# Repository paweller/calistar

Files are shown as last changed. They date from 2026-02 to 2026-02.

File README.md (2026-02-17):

# Calistar and Calitower Z

Check out the [wiki](https://github.com/dirtdigger/fleur_de_cali/wiki) for a step-by-step guide to Calistar! Calitower Z functions just the same way.

# Calistar (formerly Fleur de Cali)

Two examples 120x3 and 100x2 example

This is a free, open source, parametric tool used for adjusting the dimensional correctness and skew of your printer. This model performs a similar function to other prints such as Califlower, but has no relation to nor has been derived from any part of those. Turns out that the math behind printer skew calibration has been around since Euclid, and its application to 3D printers is well-documented on other open source project's websites like Klipper. Getting the best performance out of your printer shouldn't be behind a paywall.

Parameters you can control within the Cadquery source code:

- Number of measure points for each axis, up to 5 (default 3)
- Thickness of the grid separator pieces (default is 4mm)
- Total width of the print (default 120)
- Height of the print (default 4mm)

Features:

- Parametric design. Try this with other calibration prints: scale up the model by 20%. You'll find your print time and material used increase by up to 50% since the thickness of the print also increases. Using this design, load up a different stl to keep the thickness the same. Your print time and material used only increase by about 20%
- Bigger is better. No calipers are perfect. Printing larger calibration prints decreases the relative error of your measurements. Included is up to 180mm full size, but make sure you've got calipers that can go that large before printing.
- Multiple measurement points. Measure as many locations as you want up to three times. If you get bored of measuring, stop. If you only want to measure two outermost points since they give the highest signal-to-noise ratio, do that. The spreadsheet is smart enough to figure it out. Just make sure for every outer measurement you have a corresponding inner measurement to offset incorrect flow calibration.
- Know when to stop. Along with offsets, error estimation based on the variance of your measurements and the error in your calipers are provided. If you're probably fixing noise, the spreadsheet will tell you.

Stl and step files that are included are all 4mm tall and have varying thickness depending on the size of the print. The files are named calistar_{print width}x{number of measurements per axis}.stl.

Note about Enders and other budget printers: the movement on the x-axis is non-linear, [see here](https://klipper.discourse.group/t/correct-dimensional-accuracy/6093/5) for discussion on the matter. Calistar works on the principle that movement in each axis is linear, and therefore cannot be used to calibrate the dimensional accuracy of such printers. However, it _can_ be used to calculate and fix your printer's skew.

# Calitower Z - an addition to Calistar

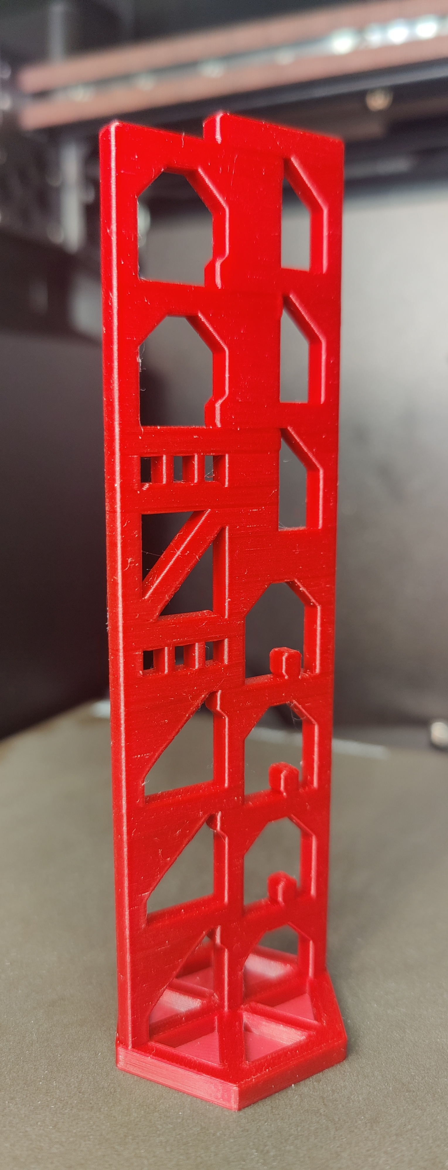
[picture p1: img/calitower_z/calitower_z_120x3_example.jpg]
Calitower Z example


Just as Calistar, Calitower Z is a free, open source, and parametric tool used to adjust a 3D printer's dimensional accuracy. While Calistar calibrates the x- and y-axis, Calitower Z sets out to do exactly that, just for the 3D printer's z-axis. Calitower Z was inspired by Calistar and is designed based on Calistar's core principles. Simply transfer the knowledge gained about Calistar to Calitower Z and you will be good to go to get your 3D printer's z-axis dialed in. Note that Calitower Z does not support a z-axis scew calibration.

__Notes on Printing__

- Use a layer height of 0.2 mm (or 0.1 mm). Otherwise, the nominal distance values between two measurement points are not guaranteed to be 120 mm, 80 mm, and 40 mm!
- Use the correct Calitowre Z version for the type of printed filament.
    - Rather stiff polymers (PLA, PETG, ABS, ASA, PC, Nylon, etc.) can easily be printed without any stiffening support structure. The correct files are the "calitower_z_stiff_<...>.<file_type>".
    - Flexible polymers (TPU, PEBA, etc.) require stiffening support structure. The correct files are the "calitower_z_flex_<...>.<file_type>".

__Notes on measuring__

- While the outer measurements are likely to represent the 3D printer's calibration quite accurately, the inner measurements might not. Even though bridging sections are kept at a minimum distance, their measurements are likely not 100 % accurate. The reasons are two-fold:
    - The droop will be ever so slight.
    - The extruded filament does not get squished against an underlying layer, but can radially extend almost equally in all directions.
    - Nevertheless, when handling these measurements diligently and taking one or two more samples per pair of measurment points, the results should be quite precise. That is at least what empirically showed.

__Notes on provided files__

- Calitower Z is currently only available in a 120x3 version. So a nominal 120 mm measurement height (144 mm print height required) with three distances for outer and inner measurements, respectively
- All the .step and .stl files provided in this repository can also be found on [printables.com](https://www.printables.com/model/1600089-calitower-z-an-addition-to-the-open-source-calista). Additionally, .3mf project as well as .bgcode presliced print files are available there.
- Regarding the calibration worksheets for Calitower Z kindly refer to the section [Browser-based calibration worksheet](#browser-based-calibration-worksheet).

# Browser-based calibration worksheet

The web-based calibration worksheet is Markdown that has been written to be compiled with [Material for Mkdocs](https://squidfunk.github.io/mkdocs-material/). A compiled version is available on [Printables](https://www.printables.com/model/778188-calistar-parametric-open-source-alternative-to-cal), simply unzip `calistar_browser.zip` and open `index.html` in a web browser.  

Note for the Calitower Z: Currently, only the "Parametric Skew Calibration.xlsx" has been modified to include dedicated input sections and output values for the z-axis. However, the browser-based version can be used just as well. Simply enter the z-measurements into either the x or y value sections and leave the rest empty. The results shown for the corresponding axis now refer to the z-axis.

# Excel-based calibration worksheet

An Excel-based calibration worksheet is included in the repo. It was created in Google Sheets, and has been tested in Excel and LibreOffice Calc. Using it with any other spreadsheet tool is unsupported and may result in errors that will not be addressed.

# License

Calistar source code and stls are distributed under GPL3 license. 

[jSpreadsheets](https://github.com/jspreadsheet/ce), [jSuites](https://github.com/jsuites/jsuites), and [Plotly Javascript](https://plotly.com/javascript/is-plotly-free/) libraries are also included in the repository, and are re-distributed under the MIT license.

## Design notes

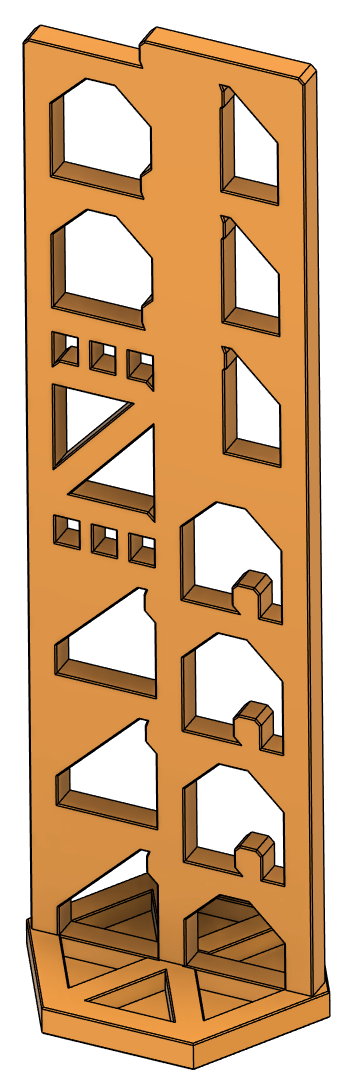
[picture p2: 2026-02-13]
img/calitower_z/calitower_z_stiff_render.png

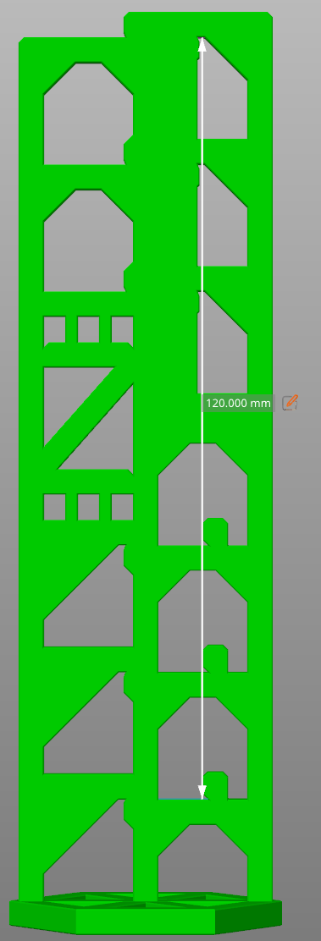
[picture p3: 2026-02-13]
img/calitower_z/calitower_z_inner_z1.png

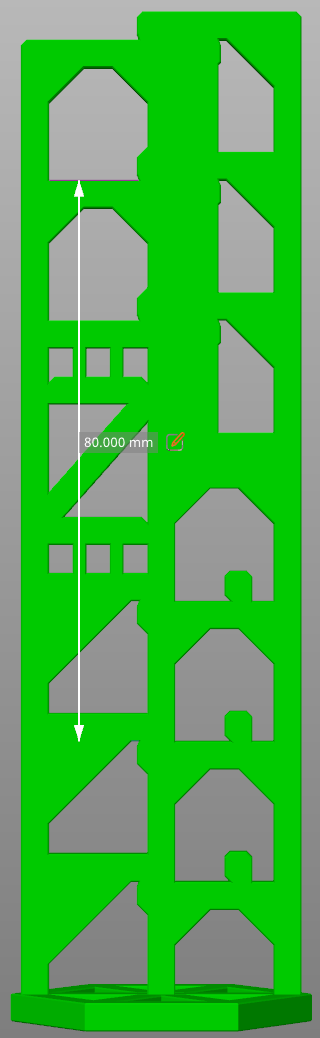
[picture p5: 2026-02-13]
img/calitower_z/calitower_z_outer_z2.png

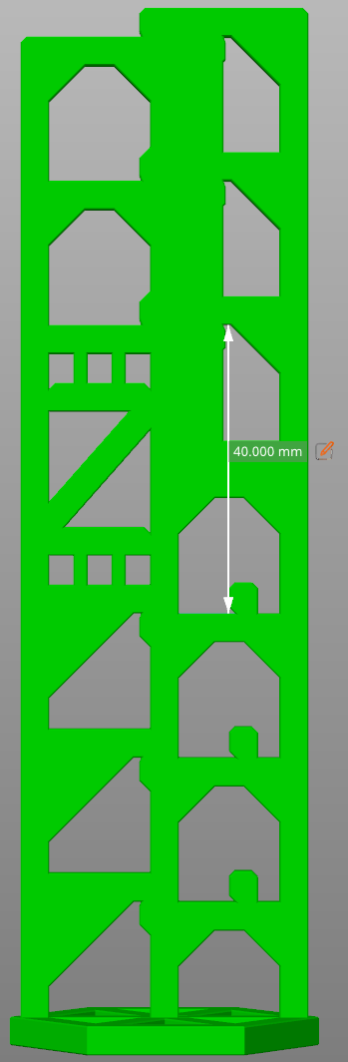
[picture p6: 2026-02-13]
img/calitower_z/calitower_z_inner_z3.png

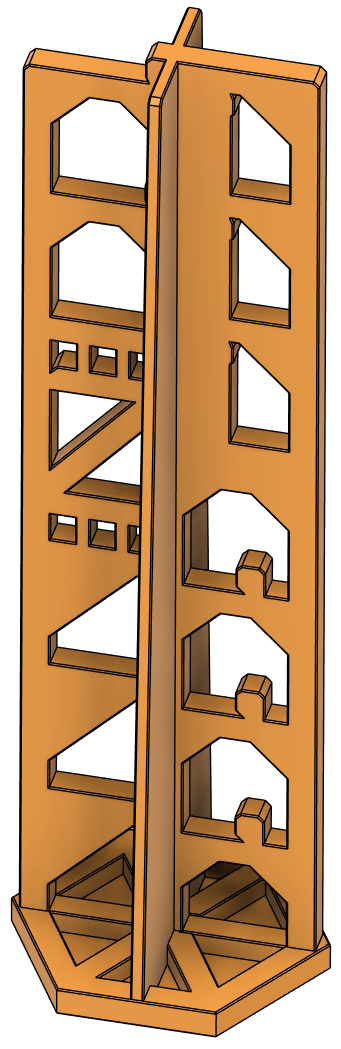
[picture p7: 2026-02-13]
img/calitower_z/calitower_z_flex_render.png

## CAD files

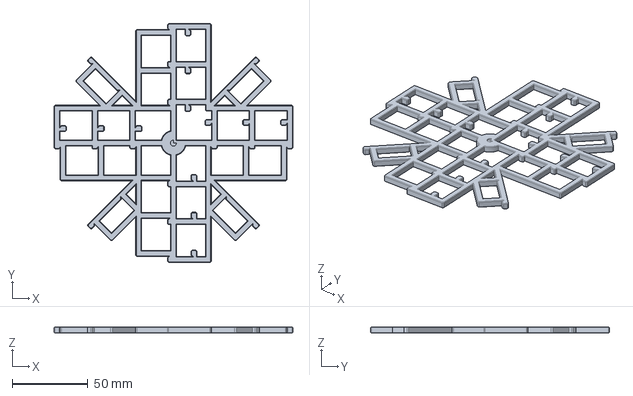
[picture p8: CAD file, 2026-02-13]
step/calistar/calistar_150x3.step
158.0 x 158.0 x 4.00 mm

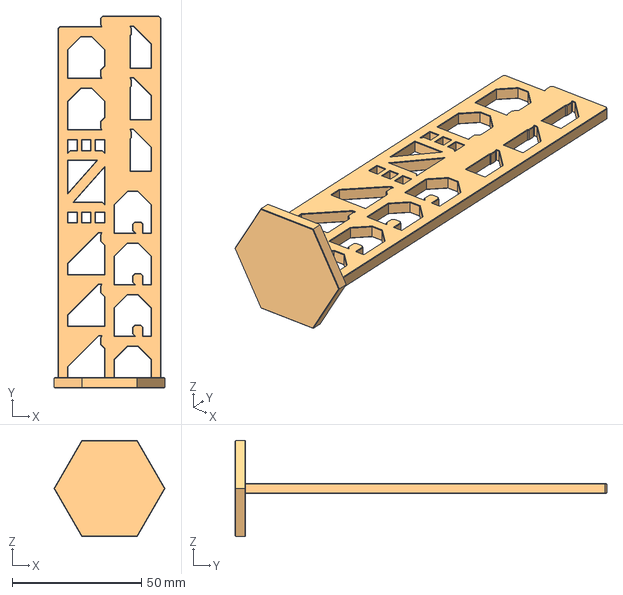
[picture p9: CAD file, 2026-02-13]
step/calitower_z/calitower_z_stiff_120x3.step
43.0 x 144.0 x 37.2 mm

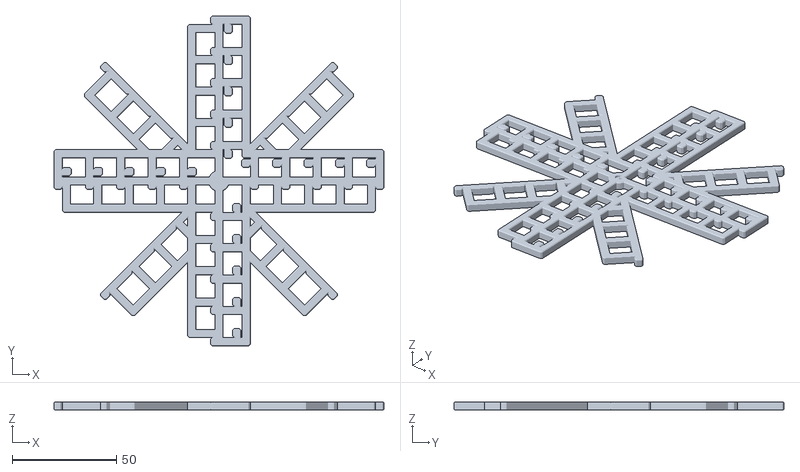
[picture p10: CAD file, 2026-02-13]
stl/calistar/calistar_150x5.stl
158.0 x 158.0 x 4.00

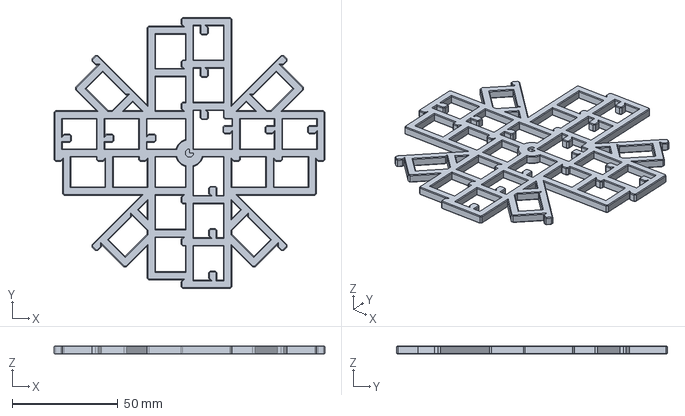
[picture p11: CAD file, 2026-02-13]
step/calistar/calistar_120x3.step
128.0 x 128.0 x 4.00 mm

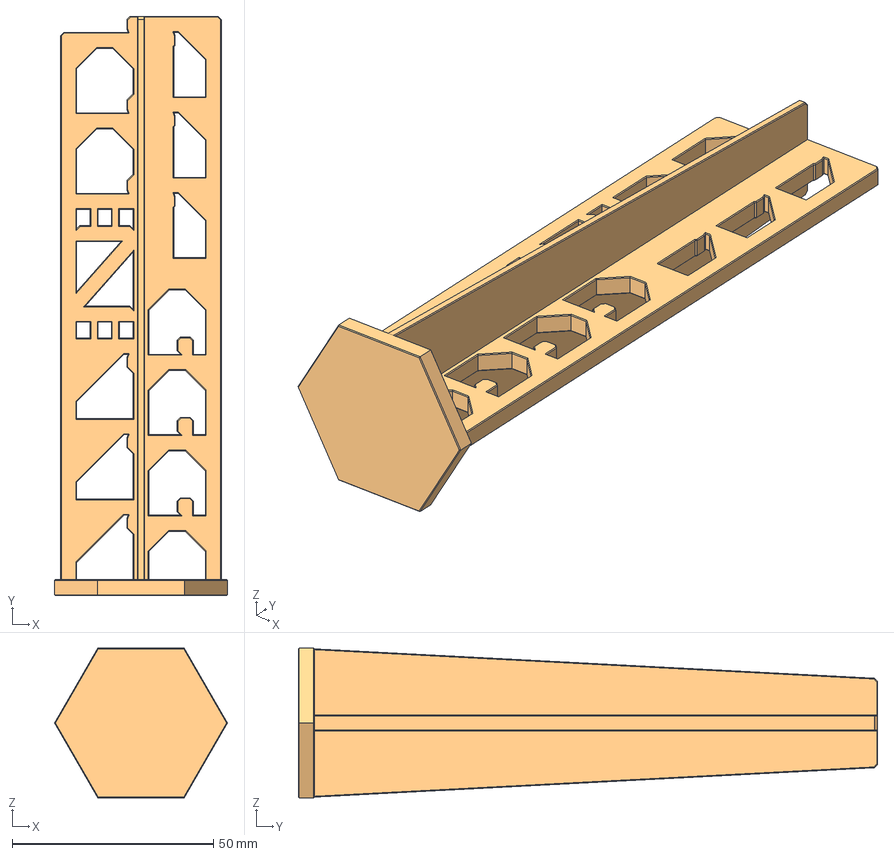
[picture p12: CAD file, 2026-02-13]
step/calitower_z/calitower_z_flex_120x3.step
43.0 x 144.0 x 37.2 mm

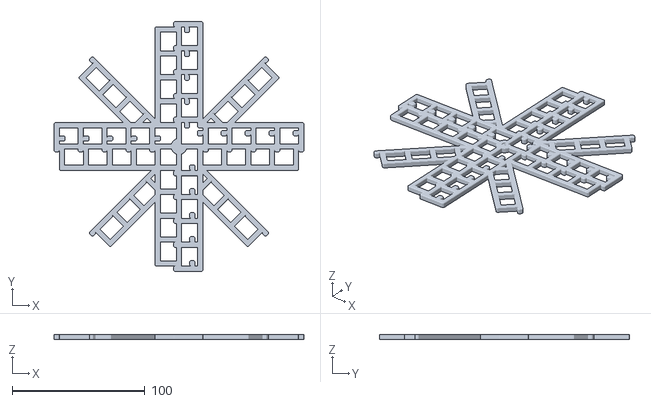
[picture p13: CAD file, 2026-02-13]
stl/calistar/calistar_180x5.stl
188.0 x 188.0 x 4.00

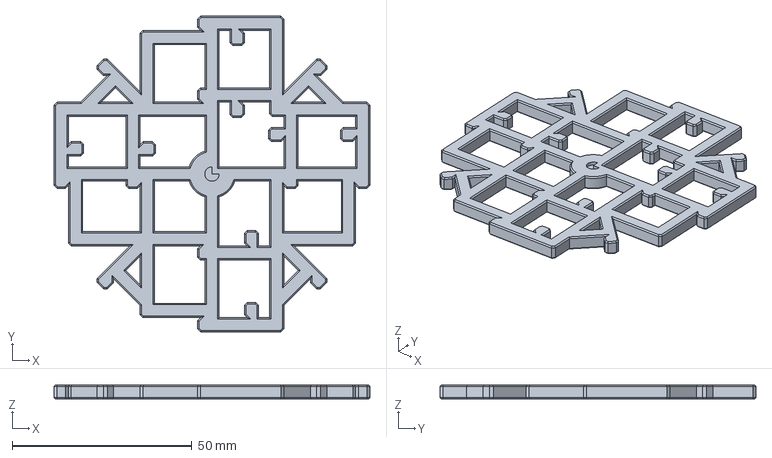
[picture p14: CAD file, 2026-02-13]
step/calistar/calistar_80x2.step
88.0 x 88.0 x 4.00 mm

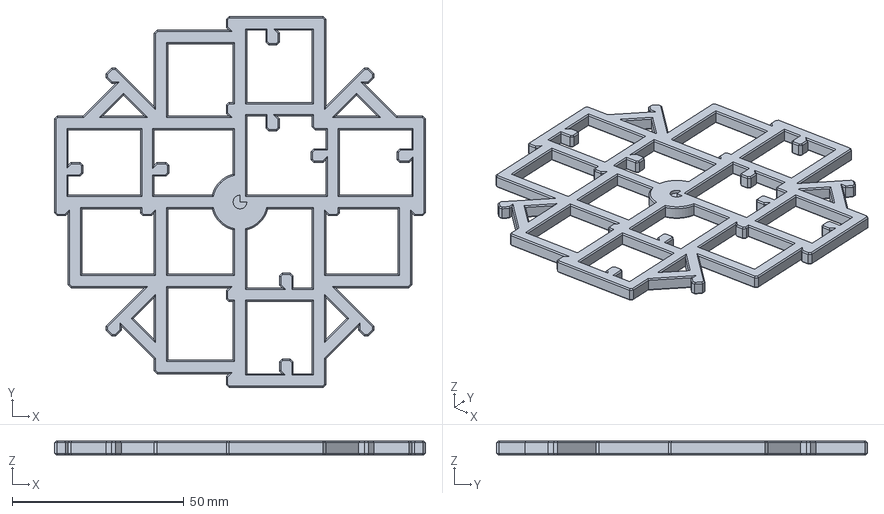
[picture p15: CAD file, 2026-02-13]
step/calistar/calistar_100x2.step
108.0 x 108.0 x 4.00 mm

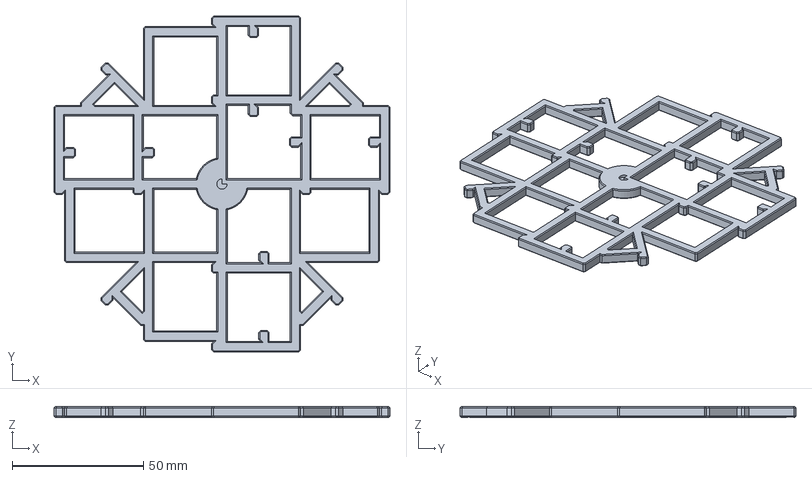
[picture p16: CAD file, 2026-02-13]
step/calistar/calistar_120x2.step
128.0 x 128.0 x 4.00 mm

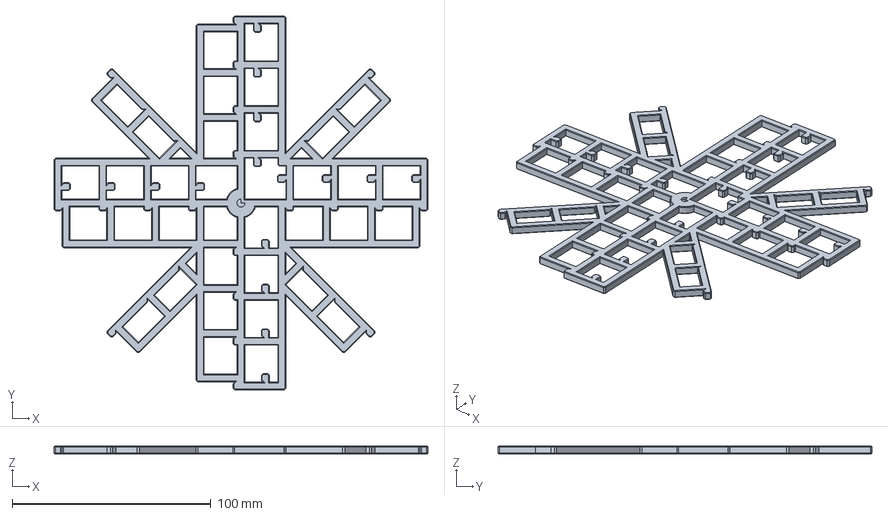
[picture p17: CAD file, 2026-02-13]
step/calistar/calistar_180x4.step
188.0 x 188.0 x 4.00 mm

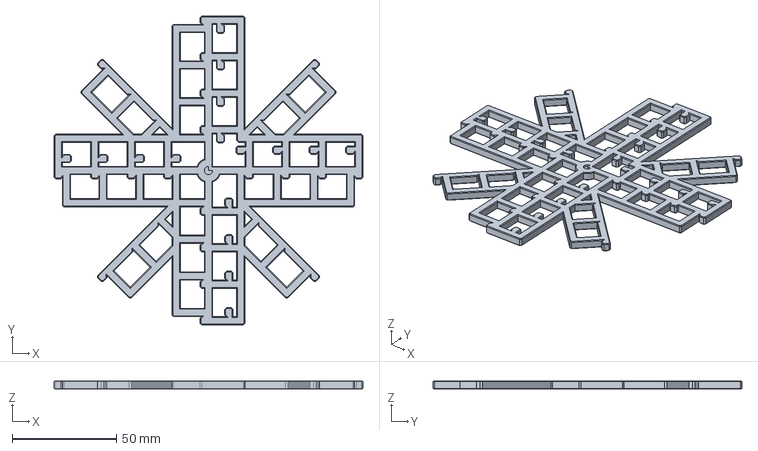
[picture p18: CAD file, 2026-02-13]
step/calistar/calistar_140x4.step
148.0 x 148.0 x 4.00 mm

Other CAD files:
stl/calistar/calistar_100x2.stl
stl/calistar/calistar_120x2.stl
stl/calistar/calistar_120x3.stl
stl/calistar/calistar_140x4.stl
stl/calistar/calistar_150x3.stl
stl/calistar/calistar_180x4.stl
stl/calistar/calistar_80x2.stl
stl/calitower_z/calitower_z_flex_120x3.stl
stl/calitower_z/calitower_z_stiff_120x3.stl

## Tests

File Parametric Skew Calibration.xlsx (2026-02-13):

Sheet: Intro
Resource before you start:
Github (always has the latest spreadsheet) (https://github.com/dirtdigger/fleur_de_cali)
Accompanying wiki for hints and tips (https://github.com/dirtdigger/fleur_de_cali)
Before you start, ensure the information below is correct
Number of measurement points | 3
Total width (mm) | 120
Scale | 1 | Did you do any additional scaling before printing the model? (Not recommended). If not, keep this as a 1
Caliper error (mm) | 0.02 | How precise your calipers are. Note: digital calipers, even though they read to the nearest 0.01mm, are often only actually accurate to 0.02mm
Use sample error | TRUE | Whether or not you want to use the measurements in the estimate of error, or just the caliper error you inputted above. You'll probably get smaller error estimates here, but they will likely be smaller than they actually are

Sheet: Post-print worksheet
Please see this wiki page for tips and measuring hints! (https://github.com/dirtdigger/fleur_de_cali/wiki/Measuring)
Tips for best results:
1. Allow the print to cool completely before measuring
2. Remove the print from the bed
Measure in this order:
 | 1. x-axis outside | (horizontal in picture)
 | 2. x-axis inside | (horizontal in picture)
 | 3. y-axis outside | (vertical in picture)
 | 4. y-axis inside | (vertical in picture)
 | 5. Diagonals | (Capital D first, then lowercase d)
 | 6. z-axis outside | (left side right picture)
 | 7. z-axis inside | (right side right picture)
Along each axis, measurements work from the outside in (see figure)
 |  | ⬐ | Hint: filter out ‘x’ values out of this column
 | Location | Nominal | Measurement 1 | Measurement 2 | Measurement 3 | Average
Outer X | 1 | 120.00
 | 2 | 80.00
 | 3 | 40.00
 |  | x
 |  | x
Inner X | 1 | 120.00
 | 2 | 80.00
 | 3 | 40.00
 |  | x
 |  | x
Outer Y | 1 | 120.00
 | 2 | 80.00
 | 3 | 40.00
 |  | x
 |  | x
Inner Y | 1 | 120.00
 | 2 | 80.00
 | 3 | 40.00
 |  | x
 |  | x
Diagonal (capital D) | 1 | 120.00
 | 2 | 80.00
 |  | x
 |  | x
diagonal (lowercase d) | 1 | 120.00
 | 2 | 80.00
 |  | x
 |  | x
Outer Z | 1 | 120.00
 | 2 | 80.00
 | 3 | 40.00
Inner Z | 1 | 120.00
 | 2 | 80.00
 | 3 | 40.00
Your measurement is within 0.5mm of expected input (does not mean your printer is calibrated!!)
Your measurement is more than 0.5mm and less than 1mm of the expected input. Please double check your measurement
Your measurement is more than 1mm away from expected input. Did you scale the model and forget to update the scale factor on intro sheet?
For best results, make sure for every outer measurement you have a corresponding inner measurement.

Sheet: Results Dimensionality
Please read this wiki page first! (https://github.com/dirtdigger/fleur_de_cali/wiki/Dimensionality)
Results
Dimensional correctness |  |  |  |  | Key
 |  | Error | 1-sigma Error | Correction | Your printer is calibrated to within one standard deviation. Hooray!
X-axis |  | #DIV/0! | 0.00000% | #DIV/0! | Your printer is calibrated to within two standard deviations. Not bad!
Y-axis |  | #DIV/0! | 0.00000% | #DIV/0! | Your printer is calibrated to within three standard deviations. You
Z-axis |  | #DIV/0! | 0.00000% | #DIV/0! |  | may still be able to do some adjustments
 |  |  |  |  | Your printer is not yet calibrated
What material did you print Calistar with?
 | Your material | Max expected shrinkage
--> Please select | PLA | 0.30%
Based on your measurements and selected material, this looks like it is most likely
#DIV/0!
Please continue scrolling to see the various ways that you can fix dimensionality of your parts
SuperSlicer, OrcaSlicer, PrusaSlicer, BambuStudio, Cura
These slicers have per-filament
shrinkage compensation built in!
Filament settings -> Filament -> Shrinkage
Enter your current shrinkage setting:
Fill me out! --> | 100 | %
Your adjusted shrinkage setting is |  | PrusaSlicer
x-, y-axis | #DIV/0! | #DIV/0!
z-axis | #DIV/0! | #DIV/0!
Generic Slicer (PrusaSlicer, SuperSlicer, BambuStudio, Cura, Simplify3D, etc.)
As a last ditch effort that works for any slicer, you can scale up your parts to account for shrinkage.
Note, however, that this must be done for every part you slice.
Your scaling factor: | x-, y-axis | #DIV/0!
 | z-axis | #DIV/0!
Fixing dimensionality in Klipper
In your printer.cfg, find and enter below
rotation_distance: | 40.000 | in [stepper_x] | <-- FIll me out!!
rotation_distance: | 40.000 | in [stepper_y] | <-- Fill me out!!
rotation_distance: | 40.000 | in [stepper_z] | <-- Fill me out!!
Your movement type: | CoreXY |  | <-- Fill me out!!
Your printer's corrected values are:
rotation_distance: | #DIV/0! | in [stepper_x] | <-- Your result
rotation_distance: | #DIV/0! | in [stepper_y] | <-- Your result
rotation_distance: | #DIV/0! | in [stepper_z] | <-- Your result
Fixing dimensionality in Marlin
In a console, type M92 into a console to get your current X- and Y-steps
X-axis | 80.000 | <-- FIll me out!!
Y-axis | 80.000 | <-- Fill me out!!
Z-axis | 80.000 | <-- Fill me out!!
Your movement type: | CoreXY | <-- Fill me out!!
In a console, paste the following:
 | #DIV/0! |  |  | <-- Your result
You should see "Recv. ok"
Then type M500 in your console to save the settings

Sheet: Results Skew
Please read the wiki first! (https://github.com/dirtdigger/fleur_de_cali/wiki/Skew)
Skew cannot currently be iteratively tuned (yet). However, this capability is in the works. Therefore, if you have already attempted to correct your skew, you should remove the correction before trying to fix it further
Skew Angle |  |  |  | Key
 | Calculated | 1-sigma Error | Correction | Your printer is calibrated to within one standard deviation. Hooray!
Angle of parallelogram | #DIV/0! | #DIV/0! |  | Your printer is calibrated to within two standard deviations. Not bad!
Skew | #DIV/0! | #DIV/0! | #DIV/0! | Your printer is calibrated to within three standard deviations. You
 |  |  |  |  | may still be able to do some adjustments
Some printers such as the Prusa i3 MK3S+ have the ability to measure this on their own. |  |  |  | Your printer is not yet calibrated
If you use such a printer, you can skip this step. Others, e.g. Bambulab printers and the Prusa
Mini, do not have a way to compensate skew. Thus this measurement is for educational
purposes only for those printers.
Fixing skew in Klipper
See the Klipper documentation for details. Please read it to understand what you are doing! (https://www.klipper3d.org/Skew_Correction.html?q=)
For your printer, use
#DIV/0!
#DIV/0!
#DIV/0!
Your skew correction gcode is:
#DIV/0!
SKEW_PROFILE SAVE=my_skew_profile
To have Klipper calculate your skew, enter this into a console:
#DIV/0!
Fixing skew in Marlin
Skew compensation coming soon!
Fixing skew in RepRap firmware
Skew compensation coming soon!

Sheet: Helper
Just some math to do the skew calculation and error propagations. Nothing to see here unles you're interested...
 | Measurement | Input Expected | Input Valid | Nominal | Sample mean | Sample stdev | Est. meas. error (mm) | Relative error | Dim. Gradient | sigma*sqrt(Grad)
Outer X | 1 | TRUE | FALSE | 0.00 |  | 0.00 | 0.02
 | 2 | TRUE | FALSE | 0.00 |  | 0.00 | 0.02
 | 3 | TRUE | FALSE | 0.00 |  | 0.00 | 0.02
 |  | FALSE | FALSE | 0.00
 |  | FALSE | FALSE | 0.00
Inner X | 1 | TRUE | FALSE | 0.00 |  | 0.00 | 0.02
 | 2 | TRUE | FALSE | 0.00 |  | 0.00 | 0.02
 | 3 | TRUE | FALSE | 0.00 |  | 0.00 | 0.02
 |  | FALSE | FALSE | 0.00
 |  | FALSE | FALSE | 0.00
Outer Y | 1 | TRUE | FALSE | 0.00 |  | 0.00 | 0.02
 | 2 | TRUE | FALSE | 0.00 |  | 0.00 | 0.02
 | 3 | TRUE | FALSE | 0.00 |  | 0.00 | 0.02
 |  | FALSE | FALSE | 0.00
 |  | FALSE | FALSE | 0.00
Inner Y | 1 | TRUE | FALSE | 0.00 |  | 0.00 | 0.02
 | 2 | TRUE | FALSE | 0.00 |  | 0.00 | 0.02
 | 3 | TRUE | FALSE | 0.00 |  | 0.00 | 0.02
 |  | FALSE | FALSE | 0.00
 |  | FALSE | FALSE | 0.00
Diagonal (D) | 1 | TRUE | FALSE | 0.00 |  | 0.00 | 0.02
 | 2 | TRUE | FALSE | 0.00 |  | 0.00 | 0.02
 |  | FALSE | FALSE | 0.00
 |  | FALSE | FALSE | 0.00
diagonal (d) | 1 | TRUE | FALSE | 0.00 |  | 0.00 | 0.02
 | 2 | TRUE | FALSE | 0.00 |  | 0.00 | 0.02
 |  | FALSE | FALSE | 0.00
 |  | FALSE | FALSE | 0.00
Outer Z | 1 | TRUE | FALSE | 0.00 |  | 0.00 | 0.02
 | 2 | TRUE | FALSE | 0.00 |  | 0.00 | 0.02
 | 3 | TRUE | FALSE | 0.00 |  | 0.00 | 0.02
Inner Z | 1 | TRUE | FALSE | 0.00 |  | 0.00 | 0.02
 | 2 | TRUE | FALSE | 0.00 |  | 0.00 | 0.02
 | 3 | TRUE | FALSE | 0.00 |  | 0.00 | 0.02
 | Skew calculation |  | Gradients and variances for skew error
 | Value | Accuracy | sigma | Gradient | sigma*sqrt(Grad)
p | #DIV/0! | #DIV/0! | #DIV/0! | #DIV/0! | #DIV/0!
q | #DIV/0! | #DIV/0! | #DIV/0! | #DIV/0! | #DIV/0!
a | #DIV/0! | #DIV/0! | #DIV/0! | #DIV/0! | #DIV/0!
b | #DIV/0! |  | #DIV/0! | #DIV/0! | #DIV/0!
cos(angle) | #DIV/0!
angle | #DIV/0!
skew | #DIV/0! |  | Dimensionality | Percentage | Cartesian steps | CoreXY steps | 1-sigma
skew standard deviation | #DIV/0! |  | X-axis | #DIV/0! | #DIV/0! | #DIV/0! | 0.0000000 |  |  | XY same?
 |  |  | Y-axis | #DIV/0! | #DIV/0! | #DIV/0! | 0 |  |  | #DIV/0!
 |  |  | Z-axis | #DIV/0! | #DIV/0! | #DIV/0! | 0 |  |  | X in shrinkage bounds?
 |  |  |  |  |  |  |  |  |  | #DIV/0!
Number of valid measurements |  |  | XY same? |  | Material | Max shrinkage percent |  | Max expected shrinkage |  | Y in shrinkage bounds?
Outer X | 0 |  | #DIV/0! |  | PLA | 0.003 |  | 0.003 |  | #DIV/0!
Inner X | 0 |  | X in shrinkage bounds? |  | PETG | 0.008 |  |  |  | Z in shrinkage bounds?
Outer Y | 0 |  | #DIV/0! |  | ABS | 0.016 |  |  |  | #DIV/0!
Inner Y | 0 |  | Y in shrinkage bounds? |  | Other | 100 |  |  |  | Probably shrinkage?
Diagonal (D) | 0 |  | #DIV/0! |  |  |  |  |  |  | #DIV/0!
diagonal (d) | 0 |  | Z in shrinkage bounds?
Outer Z | 0 |  | #DIV/0!
Inner Z | 0 |  | Probably shrinkage?
 |  |  | #DIV/0!
Klipper |  |  |  |  |  |  | Marlin
Please read the Klipper documentation to understand what you are doing! (https://www.klipper3d.org/Skew_Correction.html?q=) |  |  |  |  |  |  | In a console, paste the following:
 |  |  |  |  |  |  |  | #REF!
For your printer, your values are: |  |  |  |  |  |  | You should see "Recv. ok"
#DIV/0! |  |  |  |  |  |  | Then type M500 in your console to save the settings
#DIV/0!
#DIV/0!
Your skew correction gcode is:
#DIV/0!
SKEW_PROFILE SAVE=my_skew_profile
To have Klipper calculate your skew, enter this into a console:
#DIV/0!
In your printer.cfg, adjust
rotation_distance: | #DIV/0! | in [stepper_x]
rotation_distance: | #DIV/0! | in [stepper_y]
Marlin
In a console, paste the following:
 | #REF!
You should see "Recv. ok"
Then type M500 in your console to save the settings
Skew compensation coming soon!

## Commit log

2026-02-13 Added Calitower Z and reorganized repo accordingly
    [Parametric Skew Calibration.xlsx, calistar_100x2.step, calistar_100x2.stl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]
2026-02-17 Update README.md
    Added notes for the Calitower Z in the "Browser-based calibration worksheet" section.
